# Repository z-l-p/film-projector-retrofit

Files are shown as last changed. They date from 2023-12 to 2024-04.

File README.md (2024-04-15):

# film-projector-retrofit

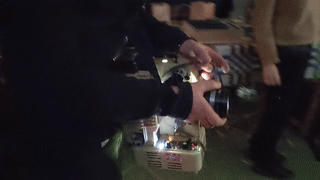
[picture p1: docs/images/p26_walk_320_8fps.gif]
Projection Performance animated GIF


This is a development platform to support the [Wandering 16mm Projector Retrofit WIKI](https://www.filmlabs.org/wiki/en/meetings_projects/spectral/mire-wandering/wandering-16mmprojection/start) on filmlabs.org. Go there for complete documentation.
=====

----

**Make a 16mm film projector portable and playable like an instrument. Retrofit with a DC motor and LED lamp, controlled by ESP32 micro-controller.**
This project is part of [SPECTRAL Wandering Sounds and Images Seminar](https://www.mire-exp.org/evenement/spectral-wandering-sound-and-images/) in Nantes FR in 2023/2024, enabling film projection performances that explore itinerancy, nomadism, and adaptation to multiple environments.

----

Contents
======

[docs](https://github.com/z-l-p/film-projector-retrofit/tree/main/docs) 
---- 

 - [Bill of Materials (BOM)](https://www.filmlabs.org/wiki/en/meetings_projects/spectral/mire-wandering/wandering-16mmprojection/budget) (filmlabs.org) or [Google Sheets alternate](https://docs.google.com/spreadsheets/d/1z_asHddtIuv7a7RkZ9WCBqF81oMiJ9spwqh7lCQfW5E) 
	
 - [Step-by-step Construction Guide](https://www.filmlabs.org/wiki/en/meetings_projects/spectral/mire-wandering/wandering-16mmprojection/construction_guide/start) for building and using the projector (filmlabs.org)
	
 - [Construction Photos](https://github.com/z-l-p/film-projector-retrofit/tree/main/docs/images)
	
 - [Diagrams](https://github.com/z-l-p/film-projector-retrofit/tree/main/docs/diagrams)
 
 - [Datasheets](https://github.com/z-l-p/film-projector-retrofit/tree/main/docs/datasheets)

[openscad](https://github.com/z-l-p/film-projector-retrofit/tree/main/openscad)
----

 - Editable design files for 3D-printed parts (in OpenSCAD format)

[projector\_code](https://github.com/z-l-p/film-projector-retrofit/tree/main/projector_code)
----

 - Code for the ESP32 micro-controller that controls the projector (Arduino IDE)

[stl](https://github.com/z-l-p/film-projector-retrofit/tree/main/stl)
----

 - Printable files for 3D-printed parts (rendered from openscad)
 
 ----
 
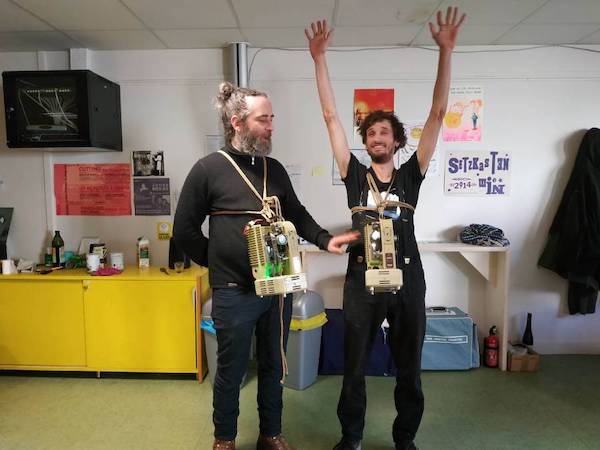
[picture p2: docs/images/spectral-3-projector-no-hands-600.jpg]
Portable Eumig P26 Projectors
 
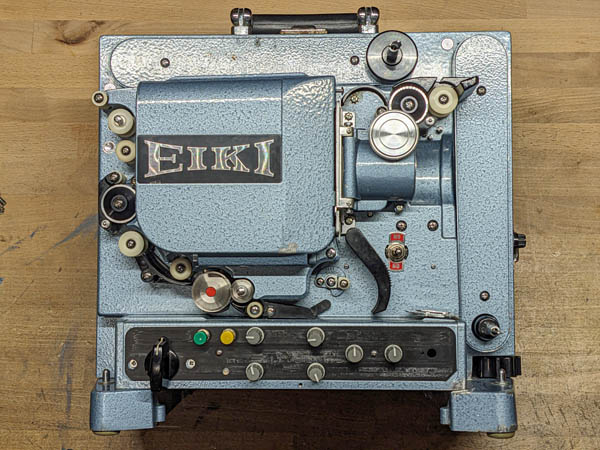
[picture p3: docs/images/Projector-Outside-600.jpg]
Eiki Projector
 
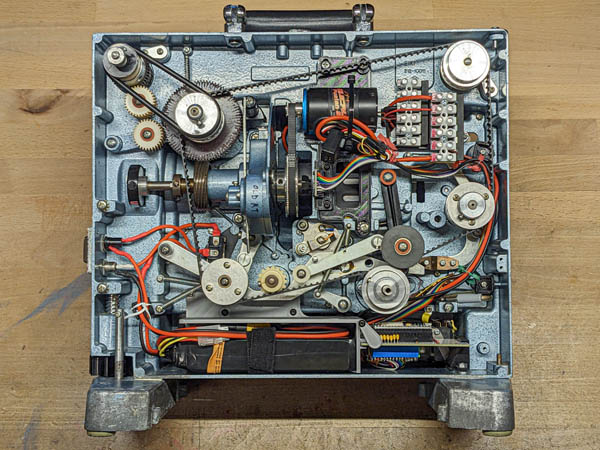
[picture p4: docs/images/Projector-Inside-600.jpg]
Eiki Projector internals


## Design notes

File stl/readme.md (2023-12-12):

The STL files for 3D-printed parts.
- **Common**: Parts used for both projectors
- **Eiki**: Parts used only on the Eiki projector
- **P26**: Parts used only on the Eumig P26 projector

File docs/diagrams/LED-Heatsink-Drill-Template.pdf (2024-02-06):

## LED Drill Template

(20mm LED, 50mm Heatsink)

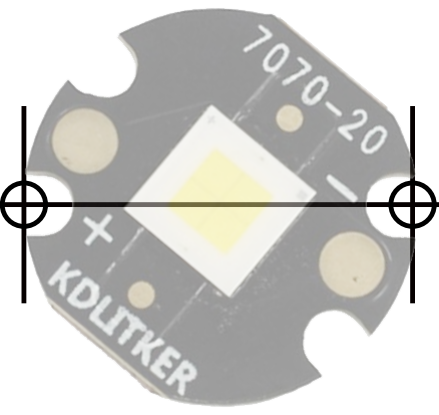
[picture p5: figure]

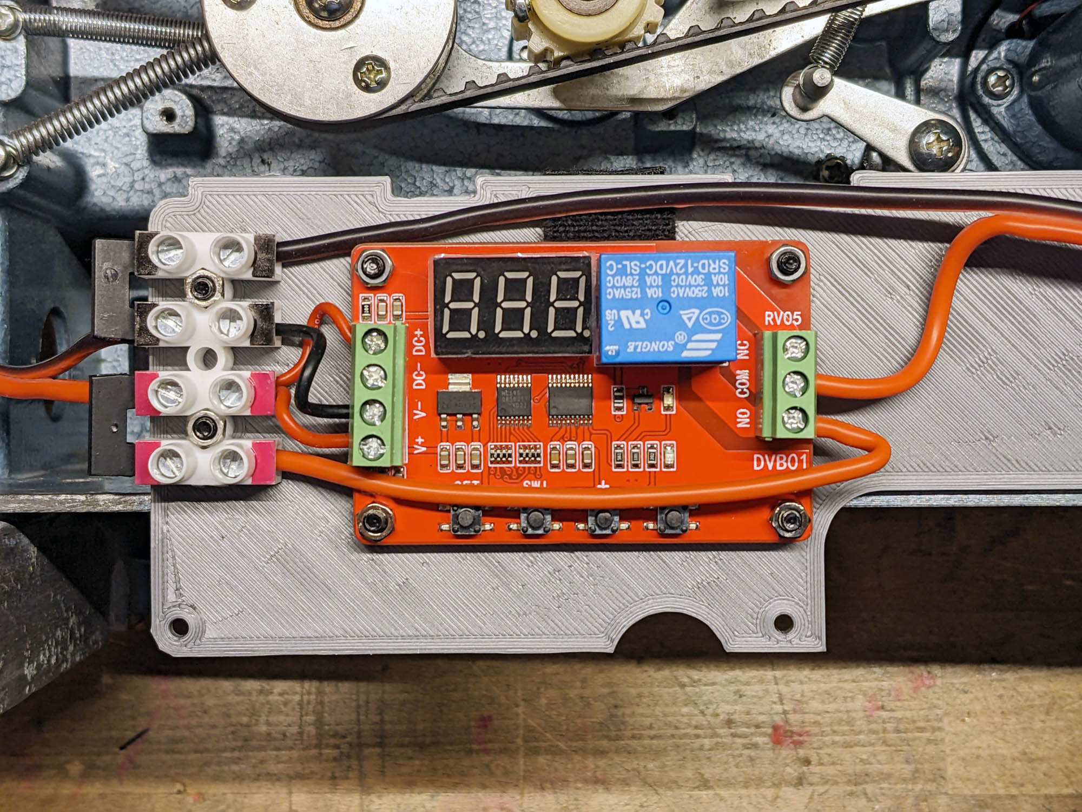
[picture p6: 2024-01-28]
docs/images/eiki-power-wiring/Power-08-protection-board-overview.jpg

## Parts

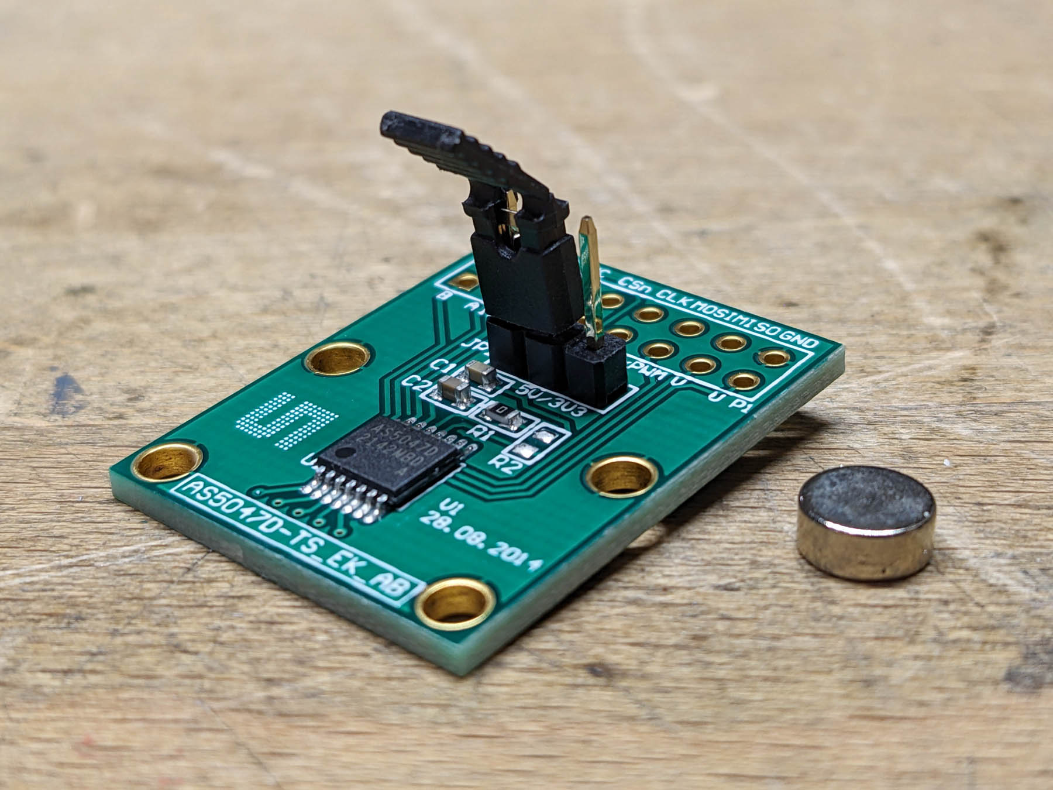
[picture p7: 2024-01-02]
docs/images/encoder/Encoder-Prep-00-parts.jpg

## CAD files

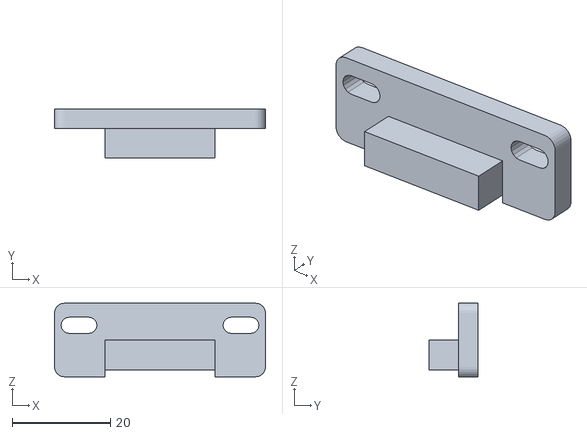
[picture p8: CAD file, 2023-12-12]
stl/Common/encoder_bracket.stl
43.0 x 10.0 x 15.0

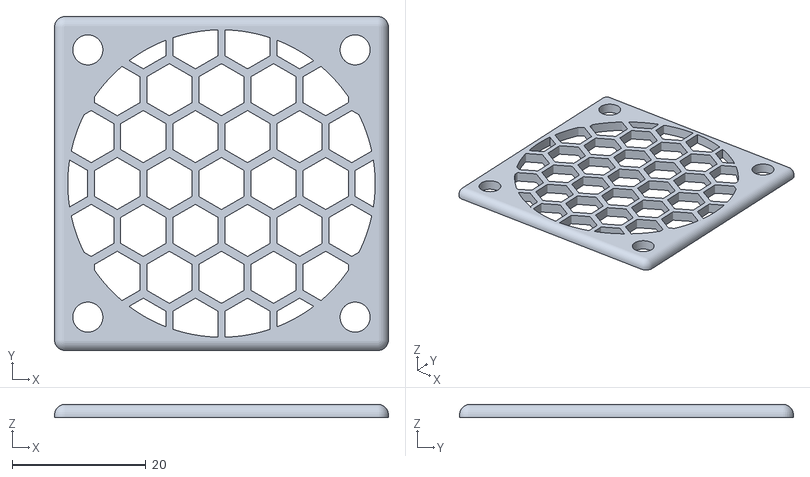
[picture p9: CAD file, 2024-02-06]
stl/Eiki/eiki_fan_guard.stl
50.0 x 50.0 x 2.00

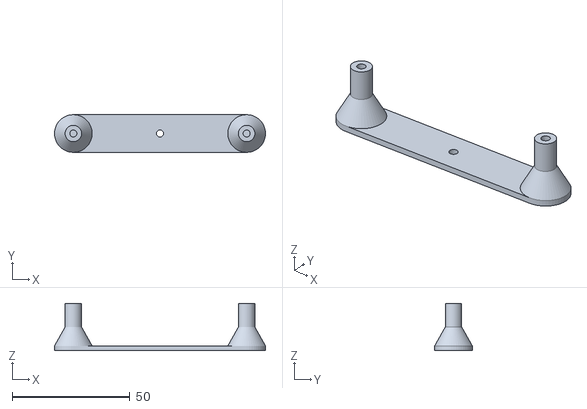
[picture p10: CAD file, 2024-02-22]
stl/P26/P26-PCB-standoff-temp.stl
89.6 x 16.0 x 20.0

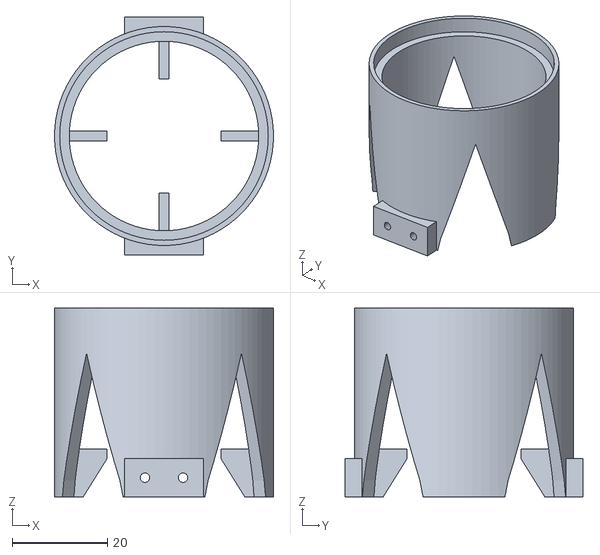
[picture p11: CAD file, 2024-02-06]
stl/Eiki/eiki_lens_holder.stl
46.0 x 50.0 x 39.6

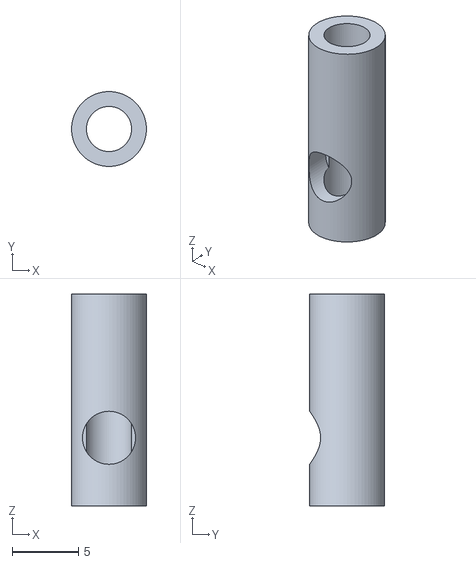
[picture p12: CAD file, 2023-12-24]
stl/P26/MotorAchsenVerbreitung.stl
5.65 x 5.65 x 16.0

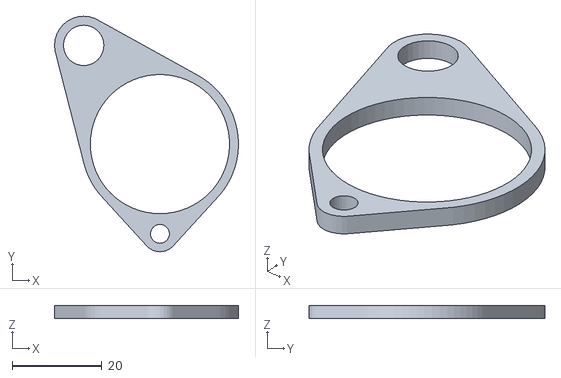
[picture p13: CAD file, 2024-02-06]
stl/Eiki/eiki_LEDdriver_tray.stl
41.0 x 52.5 x 3.00

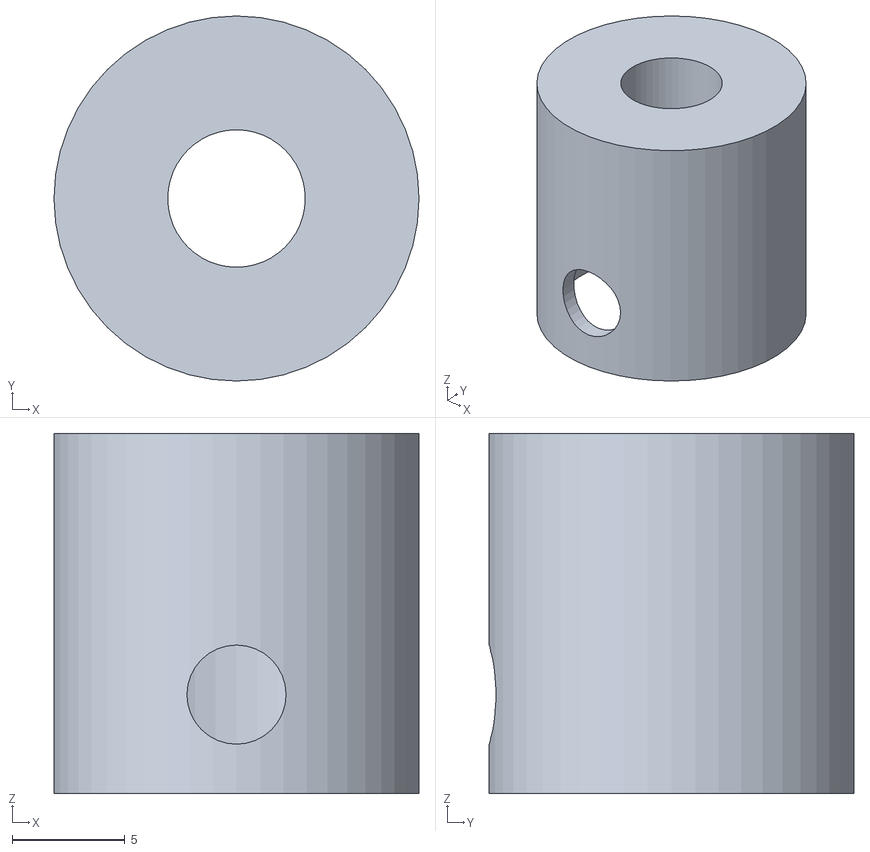
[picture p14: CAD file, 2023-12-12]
stl/P26/P26-encoder-magnet-mount.stl
16.2 x 16.2 x 16.0

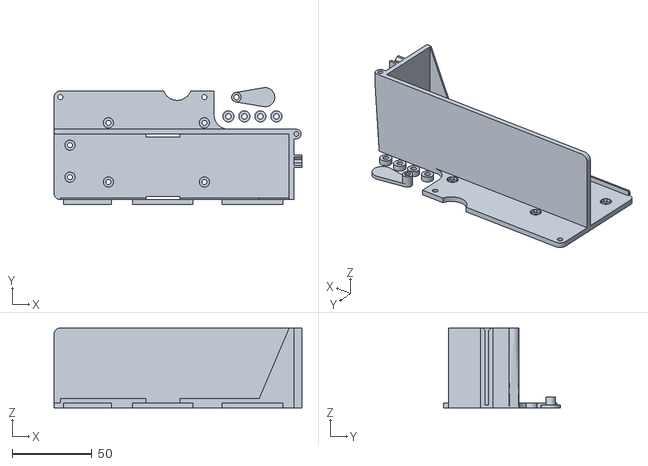
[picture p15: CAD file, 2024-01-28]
stl/Eiki/eiki_battery_box.stl
155.0 x 73.0 x 50.0

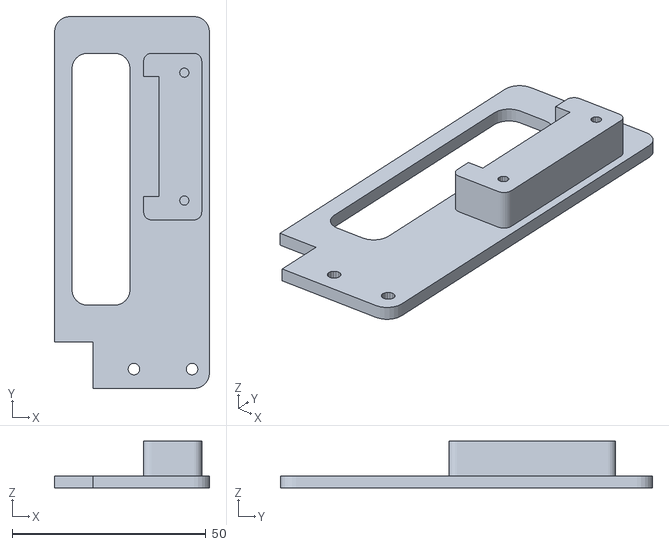
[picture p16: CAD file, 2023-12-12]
stl/P26/P26-encoder-mount.stl
40.0 x 96.0 x 12.0

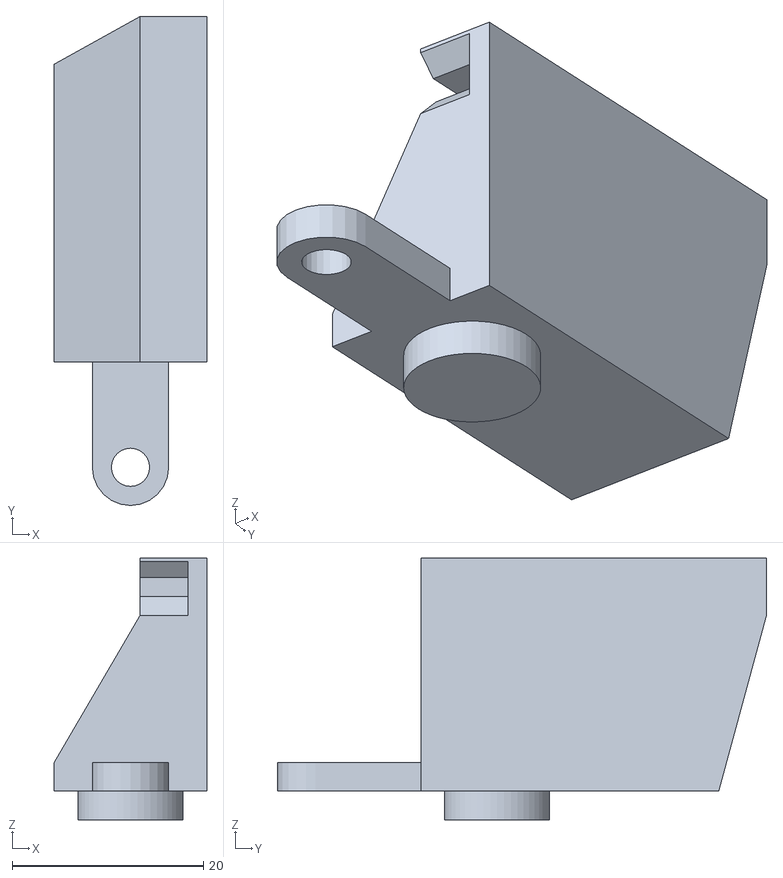
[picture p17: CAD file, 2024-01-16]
stl/Eiki/eiki_pcb_mount.stl
16.0 x 51.2 x 27.4

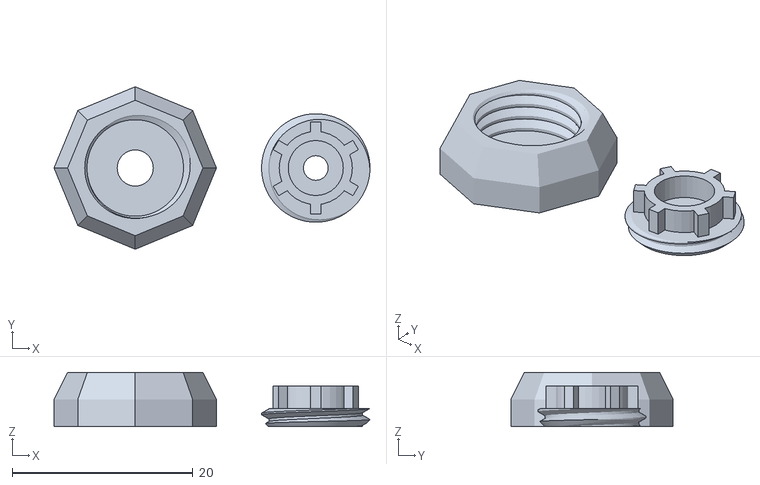
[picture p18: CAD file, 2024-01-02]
stl/Eiki/eiki_encoder_magnet_mount.stl
35.0 x 18.0 x 6.00

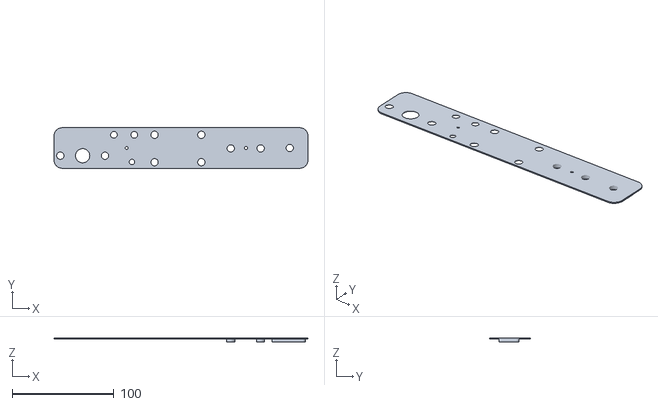
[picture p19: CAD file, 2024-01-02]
stl/Eiki/eiki_control_panel.stl
250.0 x 40.0 x 3.60

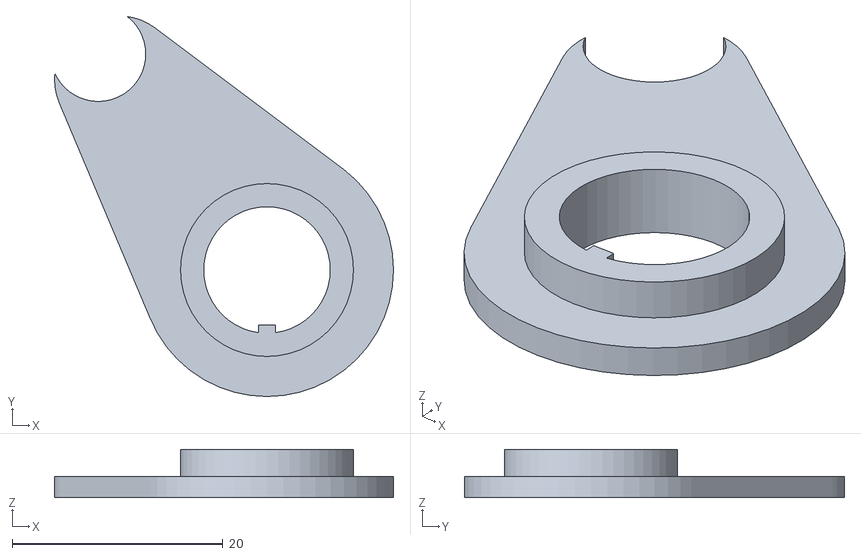
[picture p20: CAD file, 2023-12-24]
stl/Eiki/eiki_pwr_switch_adapter.stl
32.2 x 36.0 x 4.60

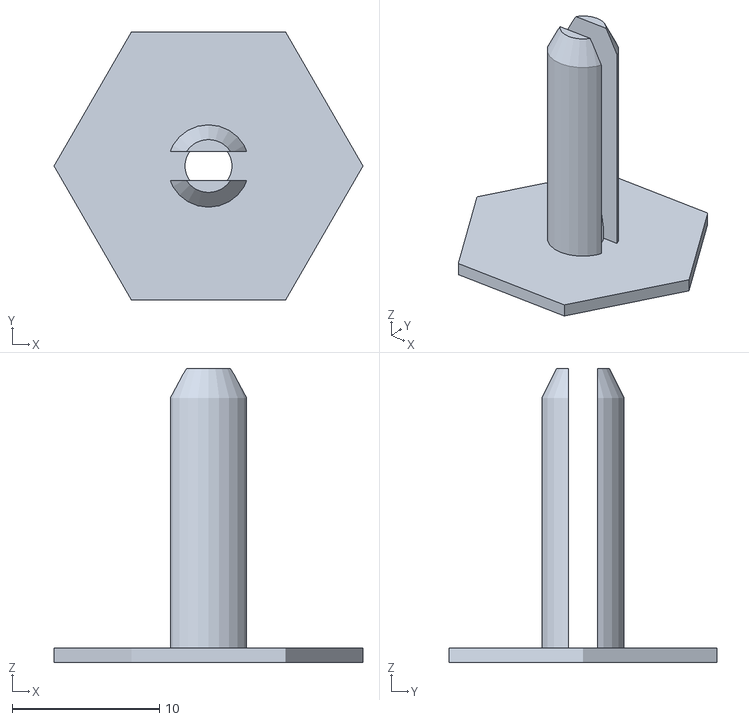
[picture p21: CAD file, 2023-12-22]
stl/Eiki/eiki_cable_clip_mount.stl
21.0 x 18.2 x 20.0

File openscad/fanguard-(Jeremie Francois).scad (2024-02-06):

//
// parametric fanguard (rev 1.01) - 20130806-1638
// (2024: modified slightly by Zach Poff for SPECTRAL Wandering project: flipped part)

// (c)Jeremie Francois (jeremie.francois@gmail.com)
//	http://www.thingiverse.com/MoonCactus
//	http://tridimake.blogspot.com
//
// Licence: Attribution - Share Alike - Creative Commons
//

// Fan size (eg. 25, 30, 40, 50 mm side length)
fan_side_length=50;

// Distance between two consecutive mounting fan screws (respectively 20, 24, 32, 40 mm)
mount_hole_width=40;

// Mounting screw diameter (respectively 3, 3, 3.5, 4.5 mm)
mount_hole_d=4.5;

// The mesh kind
mesh_kind="hex"; // [hex,square,radial_circles,radial_poly]

// The mesh cell size (mm)
mesh_holes_d=7.8;

// The mesh thickness (mm)
mesh_thickness=2;

// Additional distance between the mesh and the fan (add it to the mesh thickness for the total height) (mm)
mesh_clearance=0;

// Mesh string thickness ratio (depends on your nozzle and gcode generator); default gives about 0.8 mm (two passes)
mesh_density_ratio= 100; // [90:120]

// Minimum side wall thickness (mm)
solid_outer_border=2;

// Outer roundness (ratio over the total height; values over 50% ask for a thick wall also)
outer_roundness=80; // [0:100]

// Mesh radial offset for circular meshes (tune it for a better flow, when the outer ring is the most "open")
mesh_offset= 68; // [0:100]

tol=0.1+0;
$fa=1+0;
$fs=0.33+0;


dholes= mesh_holes_d;
marginhole= (fan_side_length-mount_hole_width)/2;
roundness= outer_roundness * (mesh_thickness + mesh_clearance) / 100;

function drot(radius, spacing)= 360 / round( (2 * 3.1415926 * radius) / spacing );

module wedge(radius,dholes)
{
	w= (drot(radius, dholes)/2) * mesh_density_ratio / 125;
	dl= (mesh_holes_d) * mesh_density_ratio / 135;
	translate([0,0,-tol])
	scale([1,1,mesh_thickness+2*tol])
	hull()
	{
		rotate([0,0,-w]) translate([radius-dl/2,0,0])	cylinder(r=0.1,$fn=4);
		rotate([0,0,+w]) translate([radius-dl/2,0,0])	cylinder(r=0.1,$fn=4);
		
		translate([radius+1.05*dl/2,0,0])	cylinder(r=0.1,$fn=4);
		
		rotate([0,0,-w]) translate([radius+dl/2,0,0])	cylinder(r=0.1,$fn=4);
		rotate([0,0,+w]) translate([radius+dl/2,0,0])	cylinder(r=0.1,$fn=4);
	}
}

rotate([180,0,0]) union()
{
	difference()
	{
		hull()
		{
			for(i=[-1,+1]) for(j=[-1,+1])
				translate([i*(fan_side_length/2-roundness),j*(fan_side_length/2-roundness),0])
					translate([0,0,roundness])
					{
						intersection() { sphere(r=roundness); translate([0,0,-roundness-tol]) cylinder(r=roundness+tol, h=roundness+tol); }
						cylinder(r=roundness,h=mesh_thickness+mesh_clearance-roundness);
					}
		}
		// Carve main section and screw holes
		translate([0,0,-tol]) scale([1,1,mesh_thickness+mesh_clearance+2*tol])
		{
			cylinder(r=fan_side_length/2-solid_outer_border);
			for(i=[-1,+1]) for(j=[-1,+1])
				translate([i*(fan_side_length/2-marginhole),j*(fan_side_length/2-marginhole),0])
					cylinder(r=mount_hole_d/2);
		}
	}

	difference()
	{
		cylinder(r=fan_side_length/2-solid_outer_border+tol, h=mesh_thickness);
		// Hey... if you find this readable, you are mad :)
		if(mesh_kind=="radial_circles" || mesh_kind=="radial_poly")
		{
			for(radius=[mesh_offset*mesh_holes_d/100:mesh_holes_d*0.95:fan_side_length/2])
				// circumference= 2*PI*radius
				for(rot=[0:drot(radius, dholes):359.9])
					rotate([0,0,rot])
						if(mesh_kind=="radial_poly")
							wedge(radius,dholes);
						else if(mesh_kind=="radial_circles")
						{
							translate([radius,0,-tol])
							cylinder(r=38*mesh_holes_d/mesh_density_ratio, h=mesh_thickness+2*tol);
						}
		}
		else // hex or square
		{
			for(i=[0:dholes:fan_side_length/2+dholes])
				for(j=[0:dholes:fan_side_length/2+dholes])
					for(si=[-1,+1]) for(sj=[-1,+1]) scale([si,sj,1])
						if(mesh_kind=="hex")
						{
							translate([i + (((j+dholes) / dholes + 1) % 2) * dholes/2 ,(j)*0.9,-tol]) // HUH!
								rotate([0,0,30])
									cylinder(r=50*mesh_holes_d/mesh_density_ratio, $fn=6, h=mesh_thickness+2*tol);
						}
						else if(mesh_kind=="square")
						{
							translate([i,j,-tol])
								cube([
									75*mesh_holes_d/mesh_density_ratio,
									75*mesh_holes_d/mesh_density_ratio,
									mesh_thickness*3+2*tol],center=true);
						}
		}
	}

}

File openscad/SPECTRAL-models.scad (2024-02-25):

// SPECTRAL "Wandering sounds + Images" projector mods
// Unless specified, all parts can print at 0.2mm layer height without supports

use <threads.scad>; // threads library from Dan Kirshner (GPL license)

////////////// GLOBAL VARIABLES ////////////////
heatsinkXY = 50; // size of LED heatsink
heatsinkZ = 20; // size of LED heatsink

////////////// GENERATE MODELS ////////////////
// (un-comment each module, render, and export STL) //

// For Eumig P26 and Eiki //
// ---------------------- //

//encoder_bracket(); // Bracket to attach encoder board - PRINT ROTATED, FLAT SIDE DOWN

// For Eiki only //
// ------------- //

//eiki_motormount(); // Mount to attach motor and rotary encoder - PRINT WITH SUPPORTS
//eiki_encoder_magnet_mount(); // 2-piece threaded part to attach encoder magnet to drive shaft - PRINT WITH 0.1mm LAYERS 
//eiki_camtank_cover(); // Cover for hole in camtank after shutter removal - PRINT ROTATED, FLAT SIDE DOWN
//eiki_LED_mount();
//eiki_LED_lens_holder(0); // export STL with 0 argument for holder, 1 argument for holder fingers
//eiki_LEDdriver_tray(); // tray to keep the LED driver in place
//projection() { // optional 2D projection of the control panel, used for SVG export for control panel label design.
eiki_control_panel(); // flat faceplate for control panel on side of projector - PRINT UPSIDE DOWN
//}
//eiki_power_switch_ring(); // adapter ring to mount power switch in hole for threading lamp
//eiki_terminal_block_mount(); // mount to hold electrical terminal blocks
//eiki_cable_clip(); // cable clip that mounts on bosses inside projector
//eiki_cable_clip_mount(); // expanding cleat to insert into large holes inside projector
//eiki_battery_box(); // battery box (with mounting points for voltage protection board and ESP32 PCB slot)
//translate([160,-64+2.6,0]) rotate([-90,0,0]) eiki_PCB_mount(); 
//eiki_PCB_mount();

// For Eumig P26 only (NOTE: Other P26 parts were created in Blender! They aren't in this file.)
// ------------------ //

//p26_encoder_magnet_mount(); // 1-piece threaded part to attach encoder magnet to drive shaft
//p26_encoder_mount(); // mount to attach encoder bracket to P26 chassis
//P26_esp_mount();


////////////// THE MODULES ////////////////

// adapter ring to mount power switch in hole for threading lamp
module eiki_power_switch_ring() {
    $fn=48;
    flangeZ = 2;
    chassisZ = 2.6;
    slotWidth = 1.6;
    holeOD = 16.4;
    holeID = 12;
    FlangeD = 24;
    
    satelliteD = 9;
    satelliteOffset = 26;
    satelliteAngle = 38;
    
    difference() {
        union() {
            hull() {
                cylinder(d=FlangeD, h=flangeZ); // outer flange
                rotate([0,0,satelliteAngle]) translate([0,satelliteOffset-3,0]) cylinder(d=satelliteD+3, h=flangeZ); // satellite flange
            }
            cylinder(d=holeOD, h=flangeZ+chassisZ); // outer
            
        }
        cylinder(d=holeID, h=10); // inner
        rotate([0,0,satelliteAngle]) translate([0,satelliteOffset,0]) cylinder(d=satelliteD, h=10); // satellite hole
    }
    
    translate([-slotWidth/2,-(holeID/2+slotWidth/2),0]) cube([slotWidth,slotWidth,flangeZ+chassisZ]); // slot guide
}

// cable clip that mounts on bosses inside projector
module eiki_cable_clip() {
    mountHoleD = 3.4;
    mountX = 15;
    mountZ = 2;
    
    difference() {
        translate([-mountX/2,-mountX/2,0]) cube([mountX,mountX,mountZ]); // base
        cylinder(d=mountHoleD, h=mountZ+1, $fn=24); // mount hole
    }
    translate([mountX/2-mountZ,0,0]) wing(); // wing1
    translate([-mountX/2,0,0]) wing(); // wing2
    translate([-mountX/2,-mountX/2,mountZ]) cube([mountX,mountZ,mountZ/2]); // side rail 1
    translate([-mountX/2,mountX/2-mountZ,mountZ]) cube([mountX,mountZ,mountZ/2]); // side rail 2
    
    module wing() {
        difference() {
            translate([0,0,mountZ]) rotate([0,90,0]) cylinder(d=mountX, h=mountZ, $fn=64); // wing cylinder
            translate([-1,0,mountZ-4.3]) rotate([45,0,0]) cube([6,6,6]); // subtract cutout
            translate([0,0,-25]) cube([50,50,50], center=true); // cut off bottom
        }
    }
}

// expanding cleat to insert into large holes inside projector
module eiki_cable_clip_mount(){
    pillarHoleD = 5.6; // inside dia of pillar hole on projector
    pillarHoleZ = 20; // depth of pillar hole on projector
    
    mountHoleD = 3.2;
    mountHoleZ = 6; // depth of mount screw hole inside this mount

    
    difference() {
        union() {
            cylinder(d=pillarHoleD, h=pillarHoleZ-2, $fn=24); // outer cylinder
            translate([0,0,pillarHoleZ-2]) cylinder(d1=pillarHoleD, d2=pillarHoleD-2, h=2, $fn=24); // outer cylinder taper
            cylinder(d=21, h=1, $fn=6); // ring
        }
        cylinder(d=mountHoleD, h=mountHoleZ-4, $fn=32); // hole
        translate([0,0,mountHoleZ-4]) cylinder(d1=mountHoleD, d2=mountHoleD-1, h=4, $fn=32); // hole top taper
        translate([-5,-(mountHoleD-1.2)/2,1]) cube([10,mountHoleD-1.2,pillarHoleZ+1]); // slit
    }
}

// mount to hold 2 electrical terminal blocks
module eiki_terminal_block_mount() {
    baseZ = 8;
    baseY = 48;
    
    term1X = 27;
    term1MountCenterX=10;
    term1OffsetY = 10;
    
    term2X = 20;
    term2MountCenterX=37;
    term2OffsetY = 5;
    term2Z = baseZ+18;
    
    mountHoleLoc = ([10,16,0]);
    mountHoleD = 3.2;
    termMountHoleD = 2.5;
    
    tabX = 33;
    tabY = 15;
    tabZ = 3;
    tabOffsetY = 20.4;
 
    // main part
    difference() {
        translate([(term1X+term2X)/2,baseY/2,0]) rounded_rect(term1X+term2X,baseY,baseZ,3); // base of terminal 1 + terminal2
        translate(mountHoleLoc) cylinder(d=mountHoleD, h=50, $fn=24); // mount hole for the object
        translate([mountHoleLoc[0],mountHoleLoc[1],3]) cylinder(d=mountHoleD*2.6, h=50, $fn=24); // pocket to clear head
        translate([term1MountCenterX,term1OffsetY,0]) term_holes(); // holes for terminal block 1
    }
    // tower for term 2
    difference() {
        translate([term1X+term2X/2,baseY/2-2,0]) rounded_rect(term2X,baseY-4,term2Z,3); // tower for terminal 2
        translate([term2MountCenterX,term2OffsetY,term2Z-8]) term_holes(); // holes for terminal block 2
        translate([0,-9,baseZ]) rotate([0,90,0]) cylinder(d=35, h=100, $fn=96); // undercut for cable clearance
    }
    // anti-rotation tab for bottom
    translate([tabX/2,tabY/2+tabOffsetY,-tabZ]) rounded_rect(tabX,tabY,tabZ,2); // anti-rotation tab

    module term_holes() {
        cylinder(d=termMountHoleD, h=50, $fn=24); // bottom mount hole for terminal strip
        translate([0,30,0]) cylinder(d=termMountHoleD, h=50, $fn=24); // top mount hole for terminal strip
    }

    

    
}

// battery box and mounting point for battery protection board
module eiki_battery_box() {
    // Origin is center of left mounting hole. Everything is relative to this!
    mountBaseX = 150; // width of main plate
    mountBaseInsideY = 64; // height of main plate interior (from mount hole center down to inside of chassis floor)
    mountBaseExtra = 8; // Extra margin on top and sides
    mountBaseZ = 3; // thickness of main plate
    mountHoleD = 3.2; // dia of screw holes for mounting this plate to chassis
    mountHoleSpan = 90; // X distance between mount holes
    
    termMountOffsetX = 6; // terminal block holes, X offset from origin 
    termMountOffsetY = 30; // top terminal block hole, Y offset from origin (lower hole will be 20mm lower)
    termMountD = 3.2; // dia of screw holes for mounting terminal blocks to this plate
    termNutHoleD = 6.6; // dia of pocket for screw heads
    
    boardMountOffsetX = 30; // upper left mount hole for DVB01, X offset from origin
    boardMountOffsetY = 16; // upper left mount hole for DVB01, Y offset from origin
    boardSpanX = 60; // X distance between holes
    boardSpanY = 37; // Y distance between holes
    
    strapX = 21; // slot for velcro strap to keep battery in place
    strapY = 2; // slot for velcro strap to keep battery in place
    strapOffsetX = 53.6;
    
    lockOffsetZ = 4.8; // height offset of PCB lock relative to top edge of wall
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

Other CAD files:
stl/Eiki/eiki_terminal_block_mount.stl
stl/Eiki/eiki_cable_clip.stl
stl/Eiki/eiki_lens_holder_clip.stl
stl/Eiki/eiki_motormount.stl
openscad/threads.scad
stl/Eiki/eiki_LED_mount.stl
stl/Eiki/eiki_camtank_cover.stl

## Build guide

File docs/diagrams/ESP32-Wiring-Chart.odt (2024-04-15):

ESP32 16mm Projector Pinout

Breadboard row numbers

Breadboard row numbers

1 | | | | | | | | | | Encoder 3.3V | | 1
2 | Blue | NeoPixel | Jumper to GPIO 15 | | | | | | Motor 6V BEC | | red | 2
3 | Red | UI 3.3V | | 3.3V | 1 | | 38 | GND | Motor GND | | brown | 3
4 | | | | EN | 2 | | 37 | GPIO23 | | Encoder SPI MOSI | White | 4
5 | White | Pot: Shutter Angle | | GPIO36 | 3 | | 36 | GPIO22 | Motor PWM OUT | | Orange | 5
6 | Grey | Pot: Shutter Blades | | GPIO39 | 4 | | 35 | X | | | | 6
7 | Purple | Pot: Lamp Slewing | | GPIO34 | 5 | | 34 | X | | | | 7
8 | Blue | Pot: Lamp Bright | | GPIO35 | 6 | | 33 | GPIO21 | Motor ESC PGM | | Yellow | 8
9 | Green | Pot: Motor Slewing | | GPIO32 | 7 | | 32 | GND | | Encoder GND | Black | 9
10 | Yellow | Pot: Motor Speed | | GPIO33 | 8 | | 31 | GPIO19 | | Encoder SPI MISO | Grey | 10
11 | Orange | Button A | | GPIO25 | 9 | | 30 | GPIO18 | | Encoder SPI CLK | Purple | 11
12 | Brown | Button B | | GPIO26 | 10 | | 29 | GPIO05 | | Encoder SPI CS | Blue | 12
13 | | (unused pin) | | GPIO27 | 11 | | 28 | GPIO17 | | Encoder I | Green | 13
14 | Purple | | Switch: Mot Forward | GPIO14 | 12 | | 27 | GPIO16 | | Encoder A | Yellow | 14
15 | Grey | | Switch: Mot Backward | GPIO12 | 13 | | 26 | GPIO04 | | Encoder B | Orange | 15
16 | Black | UI GND | Switch GND | GND | 14 | | 25 | GPIO0 | | | | 16
17 | White | | Switch: Safe Mode | GPIO13 | 15 | | 24 | GPIO02 | | LED PWM OUT | | 17
18 | | | | X | 16 | | 23 | GPIO15 | jumper | | | 18
19 | | | | X | 17 | | 22 | X | | | | 19
20 | | | | X | 18 | | 21 | X | | | | 20
21 | | Diode + jumper to Motor 6V BEC | | V IN | 19 | USB | 20 | X | | | | 21

(Grey = Analog IN pins)

Bottom of board: MALE HEADERS

Blue = 15 pin for UI

Green = 4 pin for Eiki Switch

Red = 7 pin for Motor

Yellow = 15 pin for Encoder

Top of board: FEMALE HEADERS

2x Black 19 pin for ESP32

Black 2 pin for LED PWM out

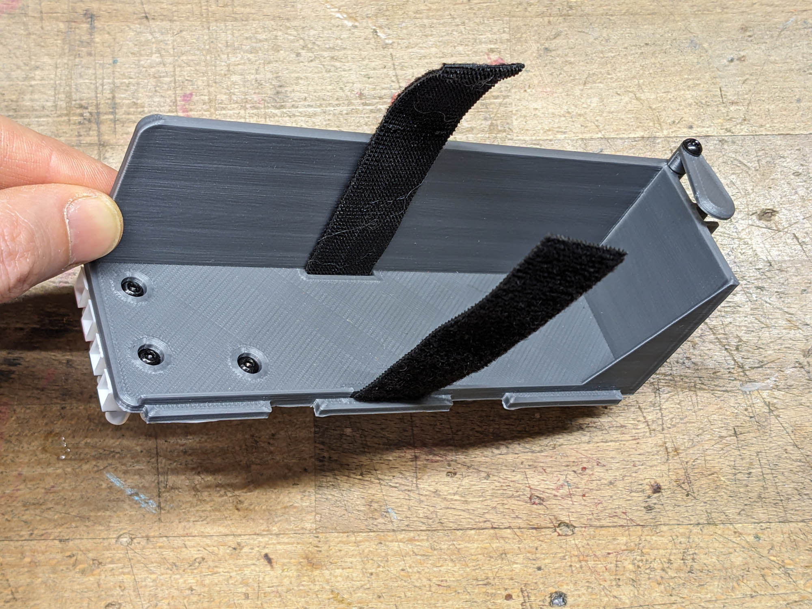
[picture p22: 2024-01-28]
docs/images/eiki-power-wiring/Power-07-batt-box-velcro.jpg

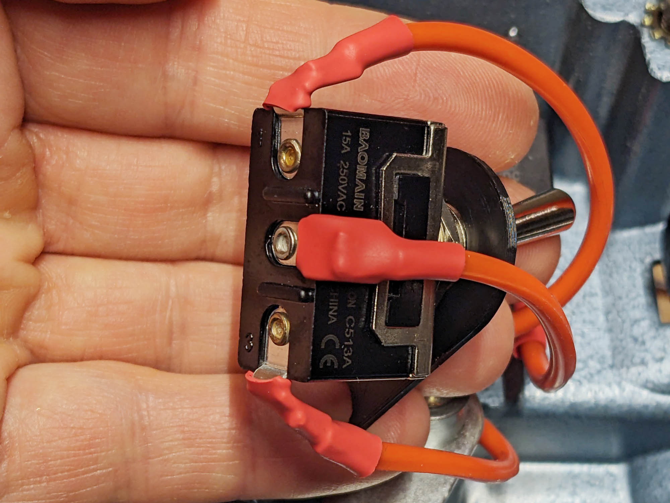
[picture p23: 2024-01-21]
docs/images/eiki-power-wiring/Power-04-switch-wiring-closeup.jpg

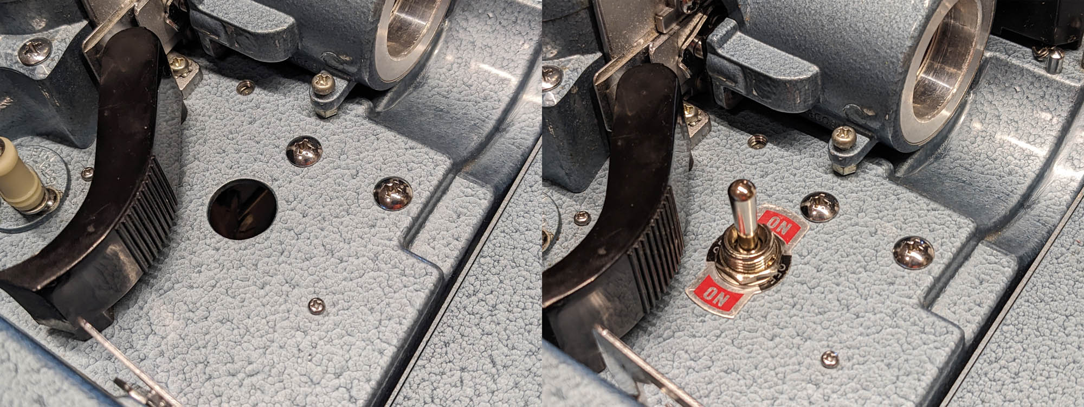
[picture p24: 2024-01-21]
docs/images/eiki-power-wiring/Power-02-switch-in-hole-before-after.jpg

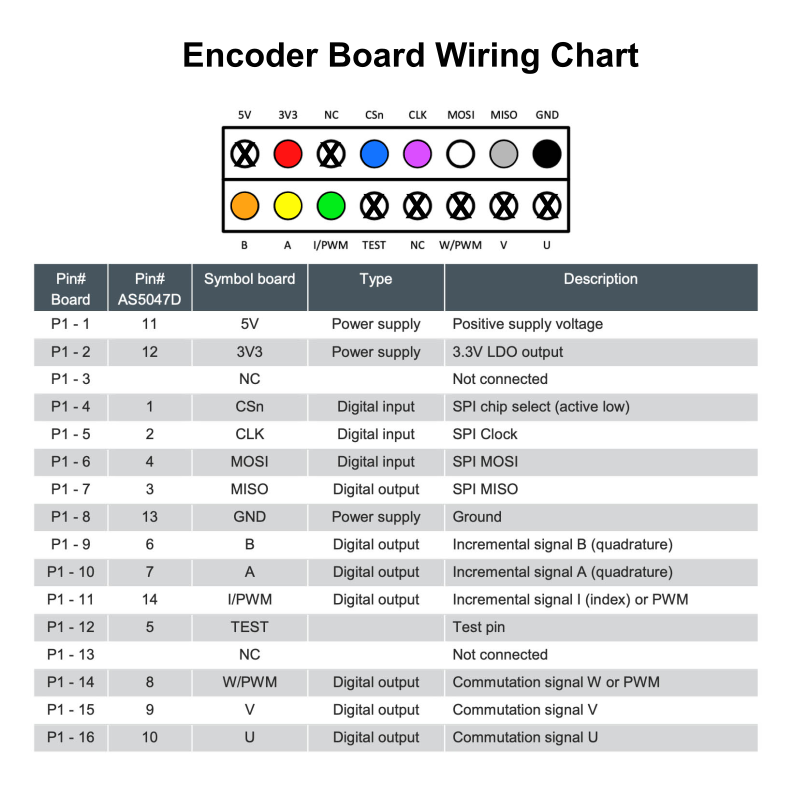
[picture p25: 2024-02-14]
docs/diagrams/Encoder-Wiring-Chart.png

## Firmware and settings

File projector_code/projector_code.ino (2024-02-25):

// ------------------------------------------
// SPECTRAL Wandering Sounds + Images Seminar
// ------------------------------------------
// Projector control software for ESP32 micro-controller
// On some 38pin ESP32 boards you need to press GPIO 0 [right] button each time you upload code. If so, solder 10uF cap between EN and GND to enable auto reset.
// Controlling Hobbywing "Quickrun Fusion SE" motor/ESC combo using ESP32 LEDC peripheral (using 16bit timer for extra resolution)
// Note: Hobbywing motor/esc needs to be programmed via "programming card" to disable braking, otherwise it will try to hold position when speed = 0
// (If you hack the ESC wiring according to our docs, you can program it with the ESCprogram() function instead of a programming card)
// "Digital shutter" is accomplished via AS5047 magnetic rotary encoder, setup via SPI registers and monitored via ABI quadrature pulses
// LED is dimmed via CC LED driver board with PWM input, driven by ESP32 LEDC (which causes slight PWM blinking artifacts at low brightness levels)
// Future option exists for current-controlled dimming (set LedDimMode=0): Perhaps a log taper digipot controlled via SPI? Probably can't dim below 20% though.


// TODO Nice but not essential:
// put UI vars in struct, in case we want to receive them from a remote ESP connected via radio
// if ESP32 Arduino core ever gets support for ledc output_invert method, we can simplify the ISR inverted condition

// Include the libraries
// NOTE: In 2023 this code was developed using the ESP32 Arduino core v2.0.9.
// When ESP32 Arduino core v3.x is released there will be breaking changes because LEDC setup will be different!
#include <AS5X47.h>         // https://github.com/adrien-legrand/AS5X47
#include <elapsedMillis.h>  // https://github.com/pfeerick/elapsedMillis
#include <Ramp.h>           // https://github.com/siteswapjuggler/RAMP
#include <SimpleKalmanFilter.h>  // https://github.com/denyssene/SimpleKalmanFilter
#include <Button2.h>             // https://github.com/LennartHennigs/Button2
#include <Adafruit_NeoPixel.h>   // https://github.com/adafruit/Adafruit_NeoPixel

// Uncomment ONE of these to load preset configurations from the matching files
#include "spectral_eiki.h" // "Store projector-specific settings here"
//#include "spectral_p26.h" // "Store projector-specific settings here"

// Debug messages. Use only one. (Warning: debug messages might cause loss of shutter sync. Turn off if not needed.)
int debugEncoder = 0;  // serial messages for encoder count and shutterMap value
int debugUI = 0;       // serial messages for user interface inputs (pots, buttons, switches)
int debugFrames = 0;   // serial messages for frame count and FPS
int debugFPSgraph = 0; // serial messages for only FPSrealAvg (for Arduino IDE serial plotter)
int debugMotor = 1;    // serial messages for motor info
int debugLed = 0;      // serial messages for LED info (LED pot val, safe multiplier, computed brightness, shutter blades and angle)

// Encoder
#define EncI 17   // encoder pulse Index (AS5047 sensor)
#define EncA 16   // encoder pulse A (AS5047 sensor)
#define EncB 4    // encoder pulse B (AS5047 sensor)
#define EncCSN 5  // encoder SPI CSN Pin (AS5047 sensor) - Library also reserves GPIO 18, 19, 23 for SPI

// OUTPUT PINS //
#define escPin 22         // PWM output for ESC
#define escProgramPin 21  // serial output to program ESC (needs 10k resistor to 3.3v)
#define ledPin 2          // PWM output for LED (On 38pin HiLetGo ESP32 board, GPIO 2 is the built-in LED)
#define NeoPixelPin 15    // output pin for NeoPixel status LED(s)

// Simple Kalman Filter Library Setup
// see tuning advice here: https://www.mathworks.com/help/fusion/ug/tuning-kalman-filter-to-improve-state-estimation.html
// and this playlist: https://www.youtube.com/watch?v=CaCcOwJPytQ&list=PLX2gX-ftPVXU3oUFNATxGXY90AULiqnWT
float kalmanMEA = 2;    // "measurement noise estimate" (larger = we assmume there is more noise/jitter in input)
float kalmanQ = 0.005;  // "Process Noise" AKA "gain" (smaller = more smoothing but more latency)

SimpleKalmanFilter motPotKalman(kalmanMEA, kalmanMEA, kalmanQ);
SimpleKalmanFilter ledPotKalman(kalmanMEA, kalmanMEA, kalmanQ);

#if (enableSlewPots)
SimpleKalmanFilter motSlewPotKalman(kalmanMEA, kalmanMEA, kalmanQ);
SimpleKalmanFilter ledSlewPotKalman(kalmanMEA, kalmanMEA, kalmanQ);
#endif

#if (enableShutterPots)
SimpleKalmanFilter shutBladesPotKalman(kalmanMEA, kalmanMEA, kalmanQ);
SimpleKalmanFilter shutAnglePotKalman(kalmanMEA, kalmanMEA, kalmanQ);
#endif

// For the FPSreal averaging
const int FPSnumReadings = 3;      // how many FPS readings to average together
float FPSAvgArray[FPSnumReadings];  // the FPS readings array
int FPSAvgReadIndex = 0;            // the index of the current reading
float FPSAvgTotal = 0;              // total of all readings


#if (enableButtons)
// Bounce2 Library setup for buttons
Button2 buttonA;
Button2 buttonB;

bool buttonAstate = 0;
bool buttonBstate = 0;
#endif

int ledSlewVal = 0;
int ledSlewValOld;
int ledSlewMin = 0;      // the minumum slew value when knob is turned down (msec).
int ledSlewMax = 10000;  // the max slew value when knob is turned up (msec).

int motSlewVal = 0;
int motSlewValOld;
int motSlewMin = 0;      // the minumum slew value when knob is turned down (msec).
int motSlewMax = 10000;  // the max slew value when knob is turned up (msec).

int shutBladesPotVal;
int shutBladesVal;
int shutBladesValOld;
int shutAnglePotVal;
float shutAngleVal;
float shutAngleValOld;


// Ramp library setup
rampInt motAvg;  // ramp object for motor speed slewing
rampInt ledAvg;  // ramp object for LED brightness slewing


#if (enableStatusLed)
  // NeoPixel library setup
#define NUMPIXELS 1  // How many NeoPixels are attached?

Adafruit_NeoPixel pixels(NUMPIXELS, NeoPixelPin, NEO_RGB + NEO_KHZ800);
// last argument should match your LED type. Add together as needed:
//   NEO_KHZ800  800 KHz bitstream (most NeoPixel products w/WS2812 LEDs)
//   NEO_KHZ400  400 KHz (classic 'v1' (not v2) FLORA pixels, WS2811 drivers)
//   NEO_GRB     Pixels are wired for GRB bitstream (most NeoPixel products)
//   NEO_RGB     Pixels are wired for RGB bitstream (5mm LEDS, v1 FLORA pixels, not v2)
//   NEO_RGBW    Pixels are wired for RGBW bitstream (NeoPixel RGBW products)
#endif

// UI VARS (could also be updated by remote control in future. Put these in a struct for easier radiolib management?)
int motPotVal = 0;  // current value of Motor pot (not necessarily the current speed since we might be ramping toward this value)
int motPotFPS = 0;  // current requested FPS based on motPotVal and scaling
int motPotFPSOld = 0;
int ledPotVal = 0;  // current value of LED pot (not necessarily the current LED brightness since we might be fading or strobing)
int ledPotValOld;

// LED VARS //
int LedDimMode = 1;              // 0 = current-controlled dimming (NOT YET IMPLEMENTED!), 1 = PWM dimming
int LedInvert = 1;               // set to 1 to invert LED output signal so it's active-low (required by H6cc driver board)
int ledBright = 0;               // current brightness of LED (range depends on Res below. If we're ramping then this will differ from pot value)
float safeSpeedMult;             // multiplier to use in "safe mode" to lower lamp brightness at low FPS
const int ledBrightRes = 12;     // bits of resolution for LED dimming
const int ledBrightFreq = 1000;  // PWM frequency (500Hz is published max for H6cc LED driver, 770Hz is closer to shutter segment period, 1000 seems to work best)
const int ledChannel = 0;        // ESP32 LEDC channel number. Pairs share settings (0/1, 2/3, 4/5...) so skip one to insure your settings work!

// MOTOR VARS We are using ESP32 LEDC to drive the RC motor ESC via 1000-2000uS PWM @50Hz (standard servo format)
int motMode = 0;                        // motor run mode (-1, 0, 1)
int motModePrev = 0;                     // previous motor run mode (-1, 0, 1)
int motSingle = 0;                       // indicates that we're traveling in single frame mode
int motSinglePrev = 0;                    // were we in single frame mode during the last loop?
int motSingleMinTime = 500;                // the minimum movement time (MS) for each single frame move
volatile int motModeReal = 0;                         // Current running direction detected by encoder (-1, 1)
float motSpeedUS = 1500;                       // speed of motor (in pulsewidth uS from 1000-2000)
const int motPWMRes = 16;                 // bits of resolution for extra control (standard servo lib uses 10bit)
const int motPWMFreq = 50;                // PWM frequency (50Hz is standard for RC servo / ESC)
int motPWMPeriod = 1000000 / motPWMFreq;  // microseconds per pulse
const int motPWMChannel = 2;              // ESP32 LEDC channel number. Pairs share settings (0/1, 2/3, 4/5...) so skip one to insure your settings work!

// prototypes for ISR functions that will be defined in later code 
// (prototype must be declared _before_ we attach interrupt because ESP32 requires "IRAM_ATTR" flag which breaks typical Arduino behavior)
void IRAM_ATTR pinChangeISR();  
void IRAM_ATTR send_LEDC();
// Start connection to the sensor.
AS5X47 as5047(EncCSN);
// will be used to read data from the magnetic encoder
ReadDataFrame readDataFrame;
volatile bool shutterMap[countsPerFrame];  // array holding values for lamp state at each position of digital shutter
volatile bool shutterStateOld = 0;       // stores the on/off state of the shutter from previous encoder position
static byte abOld;                       // Initialize state
volatile int count;                      // current rotary count
int countOld;                            // old rotary count
volatile int EncIndexCount;              // How many times have the A or B pulses transitioned while index pulse has been high
int as5047MagOK = 0;                     // status of magnet near AS5047 sensor
int as5047MagOK_old = 0;

// Machine Status Variables
volatile long frame = 0;     // current frame number (frame counter)
long frameOld = 0;           // old frame number for encoder
long frameOldsingle = 0;           // old frame number for encoder
volatile float FPScount = 0;  // measured FPS, sourced from encoder counts (100 updates per frame)
volatile float FPSframe = 0;  // measured FPS, sourced from frame counts
float FPSreal = 0; // non-volatile FPS, sourced from encoder counts at slow speeds and frame counts at high speeds
float FPSrealAvg = 0; // non-volatile measured FPS after averaging for jitter reduction
float FPStarget = 0;         // requested FPS

// Settings for HobbyWing Quicrun Fusion SE motor
#define ESC_WRITE_BIT_TIME_WIDTH 2500  // uSec length of each pulse ("2500" = 400 baud)
char ESC_settings[] = {
  0,                // RPM Throttle Matching enabled
  2,                // 3S LiPo cells
  1,                // "Low" battery cutoff threshold (Low / Med / High)
  0,                // 105C temp cutoff
  0,                // CCW rotation
  0,                // 6V BEC
  0,                // Drag brake force disabled
  4,                // Drag brake rate 5
  3,                // Max reverse force 100%
  5, 0, 4, 2, 0, 0  // extra bytes sniffed with logic analyzer, don't know what they're for
};

// timers
elapsedMicros framePeriod;  // US since last frame transition (used for FPS calc)
elapsedMicros countPeriod;  // US since last encoder count transition (used for FPS calc)
elapsedMillis timerUI;      // MS since last time we checked/updated the user interface
elapsedMillis timerFPS;      // MS since last time we checked/updated the user interface
elapsedMillis timerSingle;  // MS since single frame move began

/////////////////////////
//// ---> SETUP <--- ////
/////////////////////////

void setup() {
  Serial.begin(115200);  // Setup Serial Monitor

  pinMode(ledPin, OUTPUT);  // LEDC setup will take care of this later, but force it now just in case we're using current-controlled dimming
  digitalWrite(ledPin, 1);  // turn off LED during startup to prevent film burns

  if (enableMotSwitch) {
    pinMode(motDirFwdSwitch, INPUT_PULLUP);
    pinMode(motDirBckSwitch, INPUT_PULLUP);
  }
#if (enableButtons)
  // Attach buttons (Bounce2 library handles pinmode settings for us)
  buttonA.begin(buttonApin, INPUT_PULLUP, true);
  buttonA.setDebounceTime(5);
  buttonA.setPressedHandler(pressed);
  buttonA.setReleasedHandler(released);

  buttonB.begin(buttonBpin, INPUT_PULLUP, true);
  buttonB.setDebounceTime(5);
  buttonB.setPressedHandler(pressed);
  buttonB.setReleasedHandler(released);
#endif

  if (enableSafeSwitch) {
    pinMode(safeSwitch, INPUT_PULLUP);
  }
  if (enableShutter) {
    pinMode(EncA, INPUT);
    pinMode(EncB, INPUT);
    pinMode(EncI, INPUT);
    attachInterrupt(EncA, pinChangeISR, CHANGE);
    attachInterrupt(EncB, pinChangeISR, CHANGE);
  }

  abOld = count = countOld = 0;

#if (enableStatusLed)
  pixels.begin();                // INITIALIZE NeoPixel object
  updateStatusLED(0, 30, 0, 0);  // start with LED red while booting
#endif

  //delay(100);
  Serial.println("-----------------------------");
  Serial.println("SPECTRAL Projector Controller");
  Serial.println("-----------------------------");

// Program the ESC settings if user holds down buttonA during startup
#if (enableButtons)
  if (digitalRead(buttonApin) == 0) {
    ESCprogram();
    while (1)
      ;  // don't continue setup since the ESC needs to be rebooted before we can continue
  }
#endif



  // Set rotation direction (see AS5047 datasheet page 17)
  Settings1 settings1;
  settings1.values.dir = encoderDir;
  as5047.writeSettings1(settings1);

  // Set ABI output resolution (see AS5047 datasheet page 19)
  // (pulses per rev: 5 = 50 pulses, 6 = 25 pulses, 7 = 8 pulses)
  Settings2 settings2;
  settings2.values.abires = 6; // 25 pulses per rev = 100 transitions. This is what we want.
  as5047.writeSettings2(settings2);

  // Disable ABI output when magnet error (low or high) exists (see AS5047 datasheet page 24)
  Zposl zposl;
  Zposm zposm;
  zposl.values.compLerrorEn = 1;
  zposl.values.compHerrorEn = 1;
  as5047.writeZeroPosition(zposm, zposl);

  // This command prints the debug information to the Serial port.
  // All registers of the encoder will be read and printed.
  // as5047.printDebugString();

  // LED PWM setup (BYPASSED because we set up the LEDC on each shutter blade now, and doing it here causes LED to come on during startup)
  // if (LedDimMode) {
  //   ledcSetup(ledChannel, ledBrightFreq, ledBrightRes);   // configure LED PWM function using LEDC channel
  //   ledcAttachPin(ledPin, ledChannel); // attach the LEDC channel to the GPIO to be controlled
  //   ledcWrite(ledChannel, 1); // turn it off
  // }

  // Motor PWM setup
  ledcSetup(motPWMChannel, motPWMFreq, motPWMRes);  // configure motor PWM function using LEDC channel
  ledcAttachPin(escPin, motPWMChannel);             // attach the LEDC channel to the GPIO to be controlled

  //it's important to send the ESC a "0" speed signal (1500us) whenever the motor is stopped. Otherwise the ESC goes into "failsafe" mode thinking that our RC car has lost contact with the TX!
  ledcWrite(motPWMChannel, (1 << motPWMRes) * 1500 / motPWMPeriod);  // duty = # of values at current res * US / pulse period
  Serial.print("Sending neutral signal to ESC...");
  delay(4000);
  Serial.println("Done");

#if (enableStatusLed)
  updateStatusLED(0, 18, 16, 10);  // white LED at idle
#endif

// initialize all FPS readings to 0:
  for (int thisReading = 0; thisReading < FPSnumReadings; thisReading++) {
    FPSAvgArray[thisReading] = 0;
  }

  fixCount();                                     // at startup we don't know the absolute position via ABI, so ask SPI
  updateShutterMap(shutterBlades, shutterAngle);  //generate initial shutter map ... (1, 0.05 = 1 PPF and narrowest shutter angle)
}

/////////////////////////////////////////////
//// ---> THE LOOP (runs on core 1) <--- ////
/////////////////////////////////////////////

void loop() {
// Time-critical IO happens in interrupts, but UI and decision-making happens at a slower pace in the main loop

 //update these functions @ 200 Hz
  //  if (timerFPS >= 5) {

  //    timerFPS = 0;
  //  }

  // update these functions @ 50 Hz
  if (timerUI >= 20) {
    as5047MagCheck();  // check for encoder magnet proximity
    calcFPS();
    readUI();
    updateMotor();
    updateLed();
    timerUI = 0;
  }

  // These happen once per encoder count (only useful for debugging at slow speeds)
  if (countOld != count) {
    if (debugEncoder) {
      Serial.print("Frame: ");
      Serial.print(frame);
      Serial.print(", Frame Old: ");
      Serial.print(frameOldsingle);
      Serial.print(", Count: ");
      Serial.print(count);
      Serial.print(", Single: ");
      Serial.print(motSingle);
      Serial.print(", Lamp: ");
      Serial.print(shutterMap[count]);
      Serial.print(", Brightness: ");
      Serial.println(ledBright);
    }
    countOld = count;
  }

  // These happen once per frame (only useful for debugging)
  if (frameOld != frame) {
    if (debugFrames) {
      Serial.print("FRAME: ");
      Serial.print(frame);
      Serial.print(", FPSreal:");
      Serial.print(FPSreal);
      Serial.print(", FPS avg:");
      Serial.println(FPSrealAvg);
    }
    frameOld = frame;
  }
}

/////////////////////////////
//// ---> FUNCTIONS <--- ////
/////////////////////////////

// On interrupt, read input pins, compute new state, and adjust count
// This rotary encoder method counts all state changes (so 4x the number of "notches" on encoder) and is reliable with bouncy encoders
// From https://arduino.stackexchange.com/questions/16365/reading-from-a-ky-040-rotary-encoder-with-digispark/16420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
void IRAM_ATTR pinChangeISR() {
  enum { upMask = 0x66,
         downMask = 0x99 };
  byte abNew = (digitalRead(EncA) << 1) | digitalRead(EncB);
  byte criterion = abNew ^ abOld;
  // Execute if this is a valid transition on A or B
  if (criterion == 1 || criterion == 2) {
    //FPSreal = 10000.0 / countPeriod;  // update FPS calc based on period between the 100 encoder counts (not signed)
    //countPeriod = 0;

    // There are 3 A or B transitions during each Index pulse. (We count them here, then take action in a child loop.)
    if (digitalRead(EncI)) {
      EncIndexCount++;
    } else {
      EncIndexCount = 0;
    }
    // moving forwards ...
    if (upMask & (1 << (2 * abOld + abNew / 2))) {
      // at index
      if (EncIndexCount == 2) {  // reset counter on 'middle" transition during index condition
        count = 0;
        frame++;
        FPSframe = 1000000.0 / framePeriod;  // update FPS calc based on period between each frame
        framePeriod = 0;
      } else {
        // normal forwards count
        FPScount = 10000.0 / countPeriod;  // update FPS calc based on period between the 100 encoder counts
        countPeriod = 0;
        motModeReal = 1; // mark that we're running forwards
      }
      count++;
      // wrap around
      if (count > countsPerFrame -1) {
        count = 0;
      }
    } else {
      // moving backwards ...
      if (EncIndexCount == 2) {  // reset counter on 'middle" transition during index condition
        // at index
        count = 0;
        frame--;
        FPSframe = 1000000.0 / framePeriod;  // update FPS calc based on period between each frame
        framePeriod = 0;
      } else {
        // normal backwards count
        FPScount = 10000.0 / countPeriod;  // update FPS calc based on period between the 100 encoder counts
        countPeriod = 0;
        motModeReal = -1; // mark that we're running backwards
      }
      count--;
      // wrap around the circle instead of using negative steps
      if (count < 0) {
        count = countsPerFrame - 1;
      }
    }
  }
  abOld = abNew;  // Save new state

  // Update LED status for this encoder step

  bool shutterState = shutterMap[count];  // copy shutter state to local variable in case it changes during the ISR execution (not possible?)
  if (shutterState != shutterStateOld) {  // only update LED if shutter state changes (not every step)
    send_LEDC();                          // actual update code is abstracted so it can be run in different contexts
  }
  shutterStateOld = shutterState;  // store to global variable for next time
}
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

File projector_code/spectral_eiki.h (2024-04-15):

// Use this file to define projector-specific configurations, 
// so you don't need to modify the main code for each projector you build

// BASIC SETUP OPTIONS (enable the options based on your hardware choices)
#define enableShutter 1      // 0 = LED stays on all the time (in case physical shutter is installed), 1 = use encoder to blink LED for digital shutter
#define enableShutterPots 1  // 0 = use hard-coded shutterBlades and shutterAngle variables, 1 = use pots to control these functions
#define enableSlewPots 1     // 0 = use hard-coded ledSlewMin and motSlewMin variables, 1 = use pots to control these functions
#define motorSpeedMode 0     // 0 = motor speed is controlled by hard-coded motMinUS & motMaxUS variables, 1 = controlled by closed loop feedback
#define enableMotSwitch 1    // 0 = single pot for motor direction/speed (center = STOP), 1 = use switch for FWD-STOP-BACK & pot for speed
#define motSwitchMode 1       // if enableMotSwitch = 1, how is motor direction controlled? 
                              // 0 = (P26) Use motDirBckSwitch for FWD/REV & motDirFwdSwitch for RUN/STOP
                              // 1 = (Eiki) Use motDirFwdSwitch for RUN FWD, motDirBckSwitch for RUN REV, else STOP
#define enableSafeSwitch 1   // 0 = use hard-coded safeMode variable to limit LED brightness, 1 = use switch to enable/disable safe mode
int safeMode = 0;            // If enableSafeSwitch == 0 then use this variable: 0 = normal, 1 = ledBright is limited by speed and shutter angle to prevent film burns
const float safeMin = 0.2;       // The minimum brightness in safe mode when running very slowly / stopped
#define enableButtons 1      // 1 = use buttons A and B (for single frame FORWARD / BACK)
#define enableStatusLed 1    // 1 = use NeoPixel status LED(s) for user feedback

// INPUT PINS //
// UI
#define motPotPin 33         // analog input for motor speed pot
#define motSlewPotPin 32     // analog input for motor slew rate pot
#define ledPotPin 35         // analog input for LED dimming pot
#define ledSlewPotPin 34     // analog input for LED dimming slew rate pot
#define shutBladesPotPin 39  // analog input for # of shutter blades pot
#define shutAnglePotPin 36   // analog input for shutter angle pot
#define motDirFwdSwitch 14   // digital input for motor direction switch (forward)
#define motDirBckSwitch 12   // digital input for motor direction switch (backward)
#define buttonApin 26        // digital input for button
#define buttonBpin 25        // digital input for button
#define safeSwitch 13        // switch to enable "safe mode" where lamp brightness is automatically dimmed at slow speeds

const int countsPerFrame = 100;   // how many encoder transitions per frame
const int encoderDir = 0;   // Which magnet spin direction matches forward movement? 0 = clockwise, 1 = counter-clockwise
const float FPSmultiplier = 1; // difference between computed and actual FPS (P26 is not 1:1) 

// If (enableShutterPots == 1) then these will be reset later, but we set defaults here
int shutterBlades = 2;     // How many shutter blades: (minimum = 1 so lower values will be constrained to 1)
float shutterAngle = 0.4;  // float shutter angle per blade: 0= LED always off, 1= LED always on, 0.5 = 180d shutter angle

int motMinUS = 1800;       // motor pulse length at -24fps (set this by testing)
int motMaxUS = 1210;       // motor pulse length at +24fps (set this by testing)
int minUSoffset = 80;      // used to enforce a minumum speed when running. Otherwise low motor speed = stopped

int singleFPS = 6;        // what speed to use for film movement in single frame mode

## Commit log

2023-12-12 reorganized files
    reorganized files for future growth and Arduino IDE compatibility
2023-12-12 begin uploading 3D models
    [P26-encoder-magnet-mount.stl, P26-encoder-mount.stl, SPECTRAL-models.scad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]
2023-12-12 more 3d files
    [eiki_LED_mount.stl, eiki_camtank_cover.stl, eiki_encoder_magnet_mount.stl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]
2023-12-17 update pin numbers
    Re-ordered some UI input pins to make it easier to wire the Eiki panel
2023-12-18 update eiki control panel
    [SPECTRAL-models.scad]
2023-12-19 UI debugging + adjust pin assignments
2023-12-19 reorganize files
    [P26-encoder-magnet-mount.stl, P26-encoder-mount.stl, SPECTRAL-models.scad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]
2023-12-19 docs and pin assignments
2023-12-22 add eiki cable clip models
    [SPECTRAL-models.scad, eiki_cable_clip.stl, eiki_cable_clip_mount.stl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]
2023-12-22 Add ESC programming
    added support for ESC programming if user holds down buttonA and buttonB during startup. (Needs extra wire and pullup resistor)
2023-12-24 update power switch adapter
    [MotorAchsenVerbreitung.stl, SPECTRAL-models.scad, eiki_pwr_switch_adapter.stl]
2023-12-29 switch to RunningAverage library
    Switched from Moving Average lib to RunningAverage lib for slewing. This enables direct access to averaging array, so we can internally trim the buffer to prevent old values from re-appearing when slew pot is turned up
    [projector_code.ino]
2023-12-29 Switched slewing to Ramp library
    Finally a working solution for the slewing system. There are no longer any surprises when you turn down the slewing knobs and turn them back up. (In the past it would reveal past history in the buffer!)
    [projector_code.ino]
2024-01-01 Added enableShutter option
    In case somebody wants to retain the physical shutter, set enableShutter to 0 and the LED will stay on all the time (but remain dimmable via PWM)
2024-01-02 Add NeoPixel status LED
2024-01-02 Add NeoPixel Status LED to wiring harness and 3D files
    Also remove .01uF caps from pots (moved to PCB instead)
    [SPECTRAL-models.scad, eiki_control_panel.stl]
2024-01-02 update encoder magnet size, add LED to control panel
    [SPECTRAL-models.scad, eiki_encoder_magnet_mount.stl]
2024-01-02 docs: power wiring
2024-01-16 add batt box and PCB mount
    [SPECTRAL-models.scad, eiki_battery_box.stl, eiki_pcb_mount.stl]
2024-01-16 update BOM link in readme
2024-01-21 update power wiring images
2024-01-21 add power protection circuit (readme and images)
2024-01-22 docs - add PCB mount info
2024-01-24 clarify motor wiring image
2024-01-28 update docs, pix, models for DVB-01 power protection board
    Abandoned "ideal diode" and crowbar circuits in favor of DVB-01 relay-based power protection board. Updated the battery box model, photos, diagrams, etc
    [SPECTRAL-models.scad, eiki_battery_box.stl]
2024-01-28 updated to prepare for color-coded connectors (later)
2024-02-06 models: add fan guard & fix lens holder
    [SPECTRAL-models.scad, eiki_LEDdriver_tray.stl, eiki_fan_guard.stl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]
2024-02-06 Add LED module photos
2024-02-06 Add photo for tapped hole
2024-02-06 Docs update: Add LED and Driver, remove old power protection
2024-02-06 Code: Major changes to ADC smoothing, FPS calc
    Switched from ResponsiveAnalogRead lib to SimpleKalmanFilter lib to stop spurious noise from ADC / pots, FPSreal is now updated per encoder count (was per frame), fixed motor speed control in single pot mode (enableMotSwitch = 0) and added adjustable "deadband"
    [projector_code.ino]
2024-02-06 Docs: Added motor speed calibration
2024-02-07 safe mode: lamp dims at low FPS, turns off when stopped
    safeMin variable sets the minimum lamp brightness when projector is running slowly. (in safe mode)
    lamp turns off when motor stops (in safe mode)
2024-02-13 Docs: ESP32 diagrams and photos
2024-02-13 adjust pin numbers for pre-session3 PCB wiring
2024-02-14 Update wiring chart names
2024-02-14 Fix openscad typo, add comments
    [SPECTRAL-models.scad]
2024-02-22 models: P26 temp standoffs
    [P26-PCB-standoff-temp.stl, SPECTRAL-models.scad]
2024-02-22 code: big updates at session 3
    closed loop motor control, single framing, fixed excessive shuttermap calculations
    [projector_code.ino, spectral_eiki.h, spectral_p26.h]
2024-02-22 code: returned to manual motor control with LED FPS indicators
    also added min microsecond offset so when motor pot is at minimum there is always movement
2024-02-23 code: fixed encoder count problem, converted doubles to floats
    [projector_code.ino]
2024-02-25 CAD: Add SVG template for front panel labeling
    [SPECTRAL-models.scad]
